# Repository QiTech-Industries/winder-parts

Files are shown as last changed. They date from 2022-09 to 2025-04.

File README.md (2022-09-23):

# Winder Parts
This repository contains a part list and .stl as well as .step files for the current version of the JARVIS WINDER.

## Build the Winder
You are welcome to build your own. You just need a 3D printer and an Amazon account :D However we have no assembly instructions. The process should be pretty self-explanatory though.

We also provide the software for it, which can be found here: https://github.com/QiTech-Industries/Winder

## Improve the Winder
In case you make an improvement to one of the parts which you think may be beneficial for others as well, you are free to open a Pull Request which we are willing to merge into main. Also improvements regarding documentation/assembly instructions are welcome.
- translate the file names and part list to english
- write assembly instructions
- make the CNC Shield screw into the electronic box
- find a better solution for ESD protection than sanding down motors and profiles so they have an electrical connection
- make an excel part list with (possibly with links for buying, automatic BOM generation?)
- make the spool axis not hang from the motor shaft
- create a full CAD model (someone deleted ours :( )
- improve the friction of the puller system
- find an alternative to the TMC based tension control
- whatever you find needs improvement...

## State of the hardware
Like your see: We know that the hardware is not perfect, especially the automatic tension adjustment with the TMC2130 drivers and the friction of the puller rolls harms production. So don't expect wonders. Nevertheless we believe that this can be a good starting point in case you want to build a filament winding machine. I mean at least we successfully produced filament with it.

## No support policy
Please be aware that we can only provide support for customers that purchased a JARVIS WINDER directly from us. We have not enough resources to offer support for people that build their own (like you maybe ;). However we do our best to publish all the documentation we made internally so it should at least be possible to "puzzle" all the parts together yourself. Feel free to improve the documentation if anything has been unclear to you.

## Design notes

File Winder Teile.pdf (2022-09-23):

Heißkleber

1

Schrumpfschlauch 3cm dünn

8

Schrumpfschlauch 15cm dick

1

Schrumpfschlauch 20cm dick

1

S+W Kabel 5cm

1

Kabelbrücke

1

Kühlkörper

3

CNC Shield

1

TMC2130

3

ESPDuino ESP32

1

# Winder Elektronik

Stepper 39mm Kabel 25cm

1

Stepper 47mm Kabel 1m

1

Stepper 1:5.18 Kabel 20cm

1

Elektronik Box Basis 30g

1

Elektronik Box Deckel 30g

1

Ferrari Achsaufnahme 8g

1

Ferrari V2 25g

1

Ferrari Motorhalter 22g

1

Puller Federaufnahme unten 1g

2

Puller Federaufnahme oben 1g

2

Puller Felge Kern 3g

1

Puller Felge rund 5g

1

Puller Felge eckig 6g

1

Puller Unterlagsscheibe dünn 1g

2

Puller Querbalken 2g

1

Puller Seite 26g

2

Puller Motor Halter 4g

1

Puller Platte 25g

1

Puller Unterlagsscheibe dick 1g

2

Laserhalter 3g

1

Spool Motor Halter 15g

1

Spoolache Hero 7g

1

Spoolachse Sidekick 36g

1

Endkappe 20x40 2 Pin 2g

1

Endkappe 40x40 4Pin 5g

1

Endkappe 20x40 4 Pin 3g

3

Hohlstange l-55

1

Hohlstange d-8 l-75 Felge bei 1,6

1

Gewindestange M8 l-125

1

Linearachse d-8 l-240

1

Gewindespindel d-8 l-210

1

Linearmutter M8 l-15 d-22

1

Gewindedübel M8x28 d-10

1

Gewindebuchse M8x13

1

Eckverbinder außen 20x20

1

Gewebeschlauch 200 u-50

1

Nutensteine M5

25

T-Slot Eckverbinder 25x25

12

Aluprofil 20x40x200

4

Gummifüße d-8

4

Aluprofil 20x40x400

2

# Winder Bauteile

Mutter M4x3

5

Mutter M3x2,5

4

Netzteil 12V min. 2A

1

Box 450x350x350

1

Hama Laser

1

Nutverkleidung l-30

1

Nutverkleidung l-320

1

Nagel d-4 l-14

2

Silikonrolle l-28 d-32 d-25

2

Extruder Feder l-20 d-7,5

2

Kugellager d-8 d-22 l-7

4

Rillenkugellager d-13 d-10 l-4

3

Flex Coupler d-8 d-5 l-25

2

Flanschlager b-55 l-29 d-8

1

Linearlager d-8 d-15 l-24

1

# Winder Bauteile

Inbusschrauben M3x20

4

Inbusschraube M4x18

6

Inbusschraube M3x8

15

Inbusschraube M3x12

10

Linsenkopf breit d-11 M5x8

4

Madenschrauben M3x6

24

Senkkopf-Kreuz l-43

4

Linsenkopfschrauben M5x8

23

# Winder Schrauben

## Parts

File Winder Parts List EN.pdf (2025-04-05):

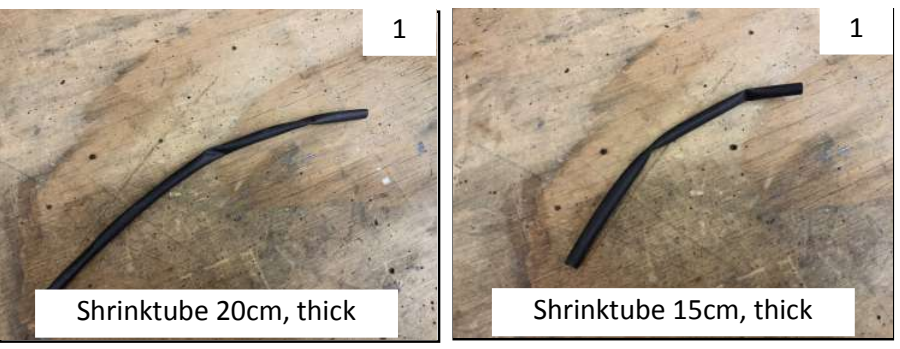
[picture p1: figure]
Shrinktube 15cm, thick; Shrinktube 20cm, thick
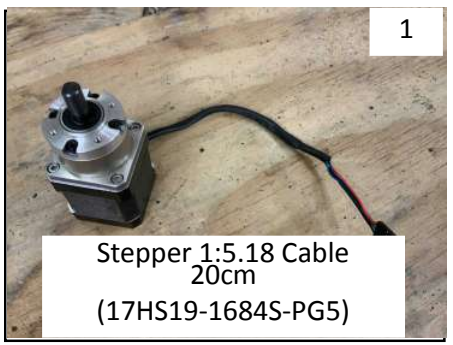
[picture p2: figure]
Stepper 1:5.18 Cable 20cm (17HS19-1684S-PG5)

Hot glue stick

1

Shrinktube 3cm, thin

8

Black+White Cable 5cm

1

Pitch Jumper Cap

1

Heat sink
(sometimes included with TMC2130)

3

A4988 Driver CNC Shield

1

TMC2130 stepper motor driver

3

ESPDuino ESP32 D1R32 Wemos

1

# Winder Electronic Parts

Stepper 47mm Cable 1m
(17HS19-2004S1)

2

Electronics Box Base 30g

1

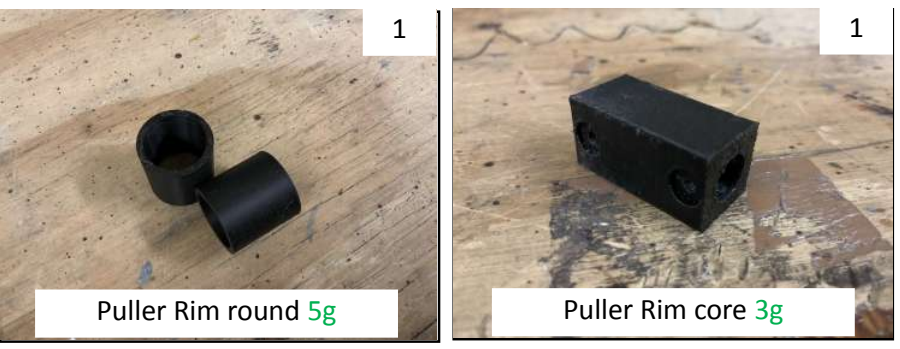
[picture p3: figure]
Puller Rim core 3g; Puller Rim round 5g

Electronics Box Lid 30g

1

Ferrari Axle Holder 8g

1

Ferrari with V-groove bearings 25g

1

Ferrari Motorholder 22g

1

Puller Spring holder Bottom 1g

2

Puller Spring Holder top 1g

2

Puller Rim square 6g

1

Puller Washer thin 1g

2

Puller Crossbar 2g

1

Puller Side 26g

2

Puller Motor Holder 4g

1

Puller Plate 25g

1

# Winder Printed Parts

Spool Motor Holder 15g

1

Spoolaxle Hero 7g

1

Spoolaxle Sidekick 36g

1

Endcap 20x40 2 Pin 2g

1

Endcap 40x40 4Pin 5g

1

Endcap 20x40 4 Pin 3g

3

# Winder Printed Parts

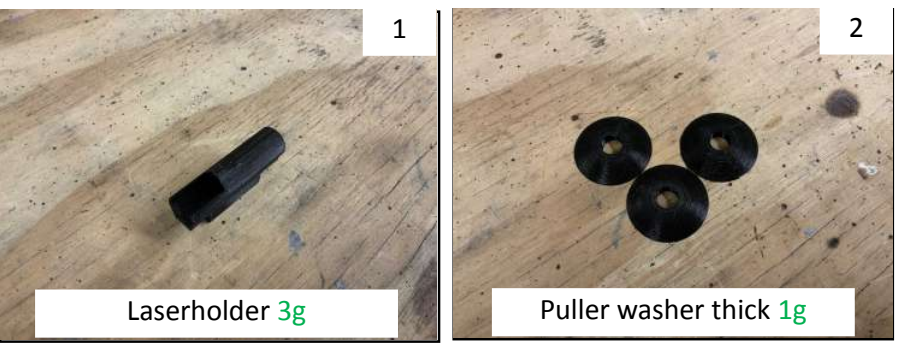
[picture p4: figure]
Puller washer thick 1g; Laserholder 3g

Hollow tube D-8 L-55

1

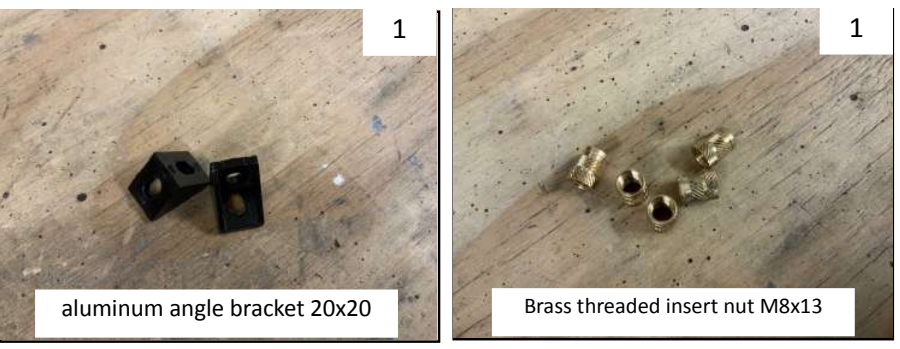
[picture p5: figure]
Brass threaded insert nut M8x13; aluminum angle bracket 20x20

Hollow tube D-8 L-75 Thickness 1.6

1

Threaded rod M8 L-125

1

Linear axle/Rod D-8 L-240

1

T8 Lead screw D-8 L-210

1

Brass nut for T8 lead
screw
M8 L-15 D-22

1

Drop in expansion anchor M8x28 OD-10

1

Braided Sleeving 200mm u-50

1

T-nut M5

25

T-slot L-type 90 degree
2020 aluminum connector
25x25

12

V-slot ALU extrusion
profile
20x40x200

4

Rubber feet D-8

4

V-slot ALU extrusion
profile
20x40x400

2

# Winder Parts

Nut M4x3

5

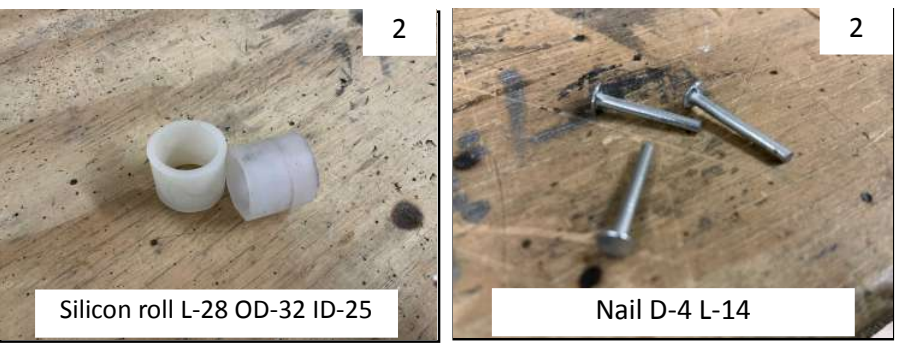
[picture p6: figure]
Nail D-4 L-14; Silicon roll L-28 OD-32 ID-25

Nut M3x2,5

4

Mains power converter to 12V min. 2A

1

Box 450x350x350

1

Hama Laser

1

Insulation sleeve l-30

1

Insulation sleeve l-320

1

Puller spring L-20 D-7,5

2

Ball bearing ID-8 OD-22 L-7 (608zz)

4

Deep groove ball bearing OD-13 ID-10 L-4

3

Flex coupler ID-8 to ID-5 L-25

2

Pillow block ball bearing KP08 8mm B-55 L-29 ID-8

1

Linear bearing ID-8 OD-15 L-24

1

# Winder Parts

Hex Socket Head Cap bolt M3x8

15

Hex Socket Head Cap bolt M3x12

10

Wide Button Head Hexagon Socket bolt D-11 M5x8

4

Hex socket set screw M3x6

24

flat head countersunk, phillips, L-43 M3

4

Button Head Hexagon Socket bolt M5x8

23

# Winder Screws & Bolts

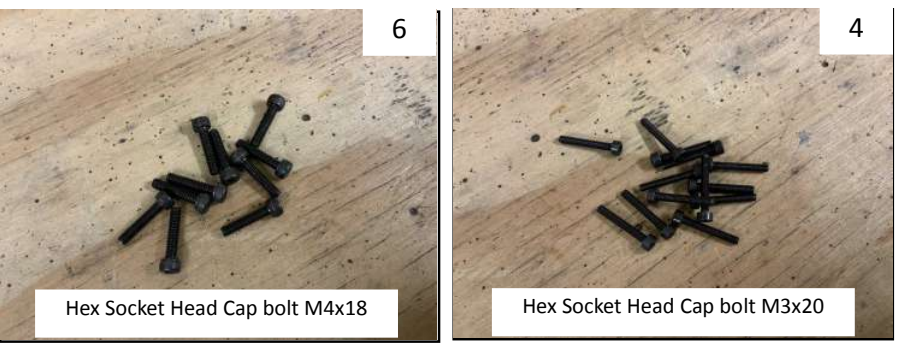
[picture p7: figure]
Hex Socket Head Cap bolt M3x20; Hex Socket Head Cap bolt M4x18

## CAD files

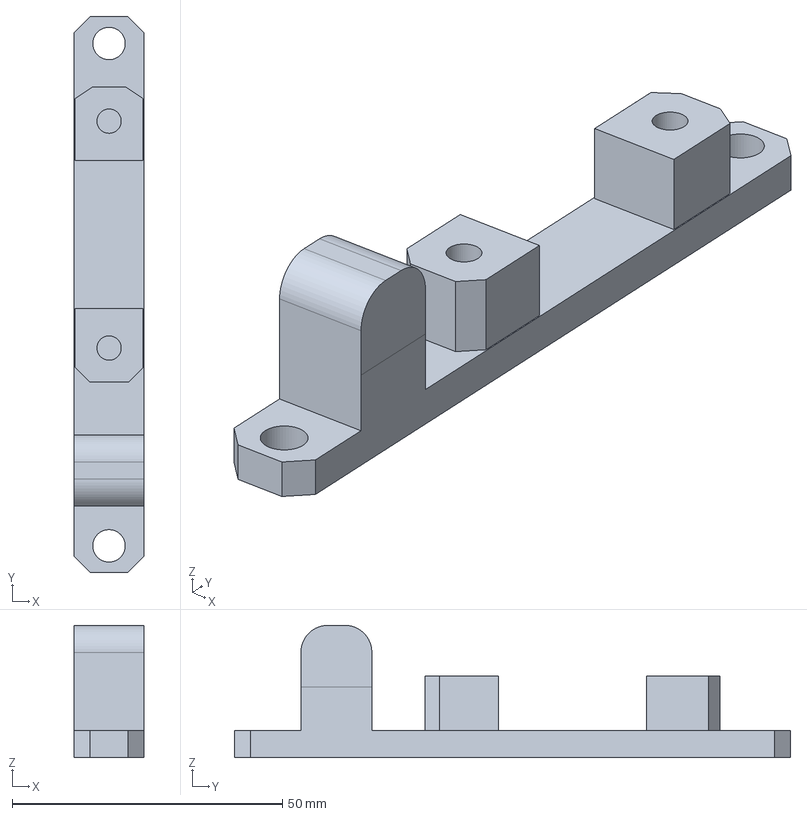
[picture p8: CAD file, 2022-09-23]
STEP/Ferrari Achsaufnahme.step
13.0 x 102.9 x 24.5 mm

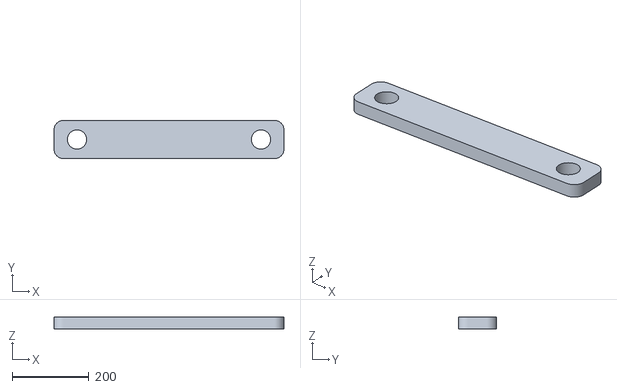
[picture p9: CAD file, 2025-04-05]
STL/STL-EN-UPDATED/Puller Crossbar.stl
600.0 x 99.8 x 30.0

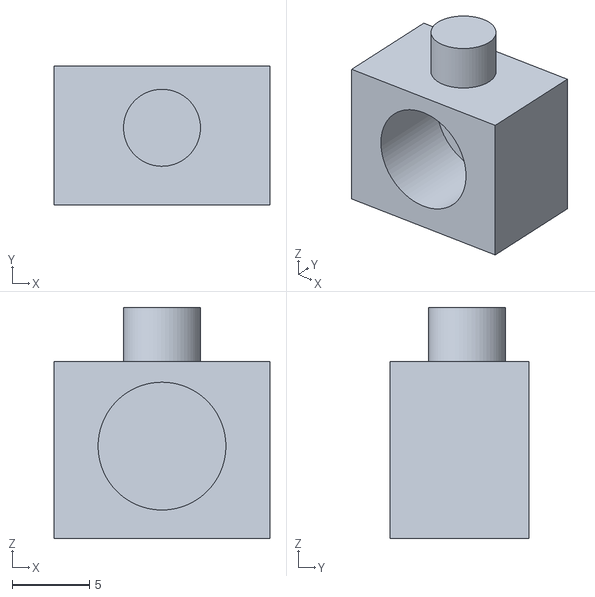
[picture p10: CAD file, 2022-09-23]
STL/STL-GER-ORIGINAL/Puller Federaufnahme unten.stl
14.0 x 9.00 x 15.0

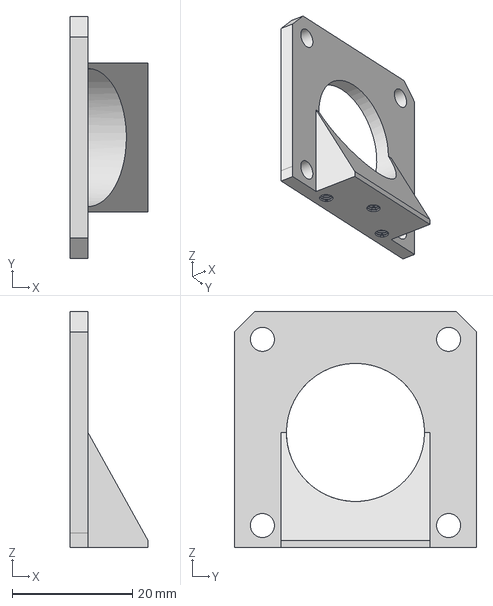
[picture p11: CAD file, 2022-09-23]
STEP/Puller Motor Halter.step
13.0 x 40.3 x 39.3 mm

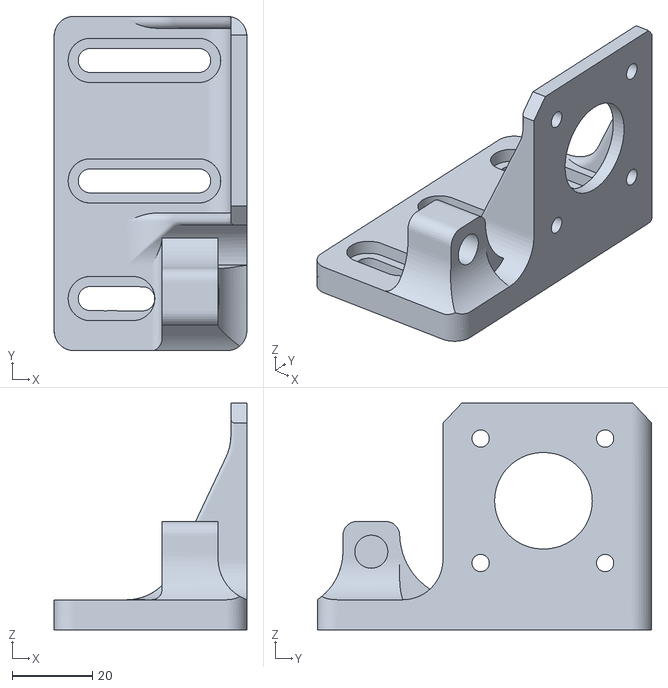
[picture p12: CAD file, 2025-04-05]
STL/STL-EN-UPDATED/Ferrari Motor Holder.stl
48.0 x 83.3 x 56.5

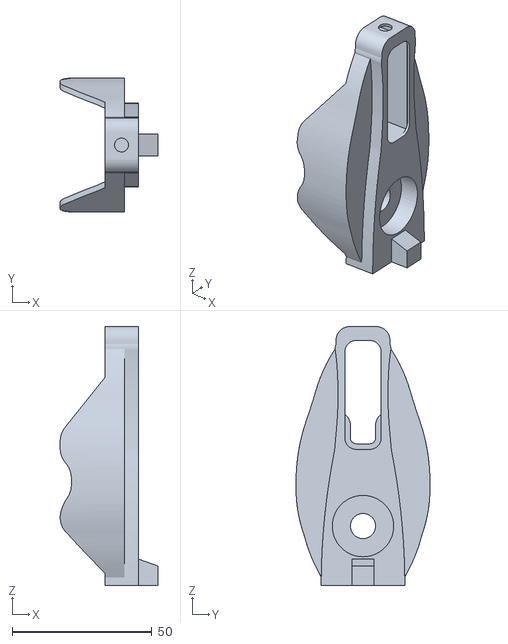
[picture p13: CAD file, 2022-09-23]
STL/STL-GER-ORIGINAL/Puller Seite Rechts.stl
35.0 x 48.0 x 92.8

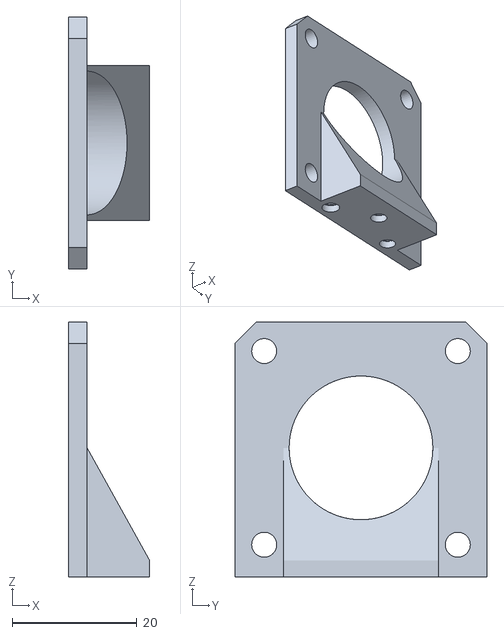
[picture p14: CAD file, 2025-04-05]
STL/STL-EN-UPDATED/Puller Motor Holder.stl
13.0 x 40.3 x 40.8

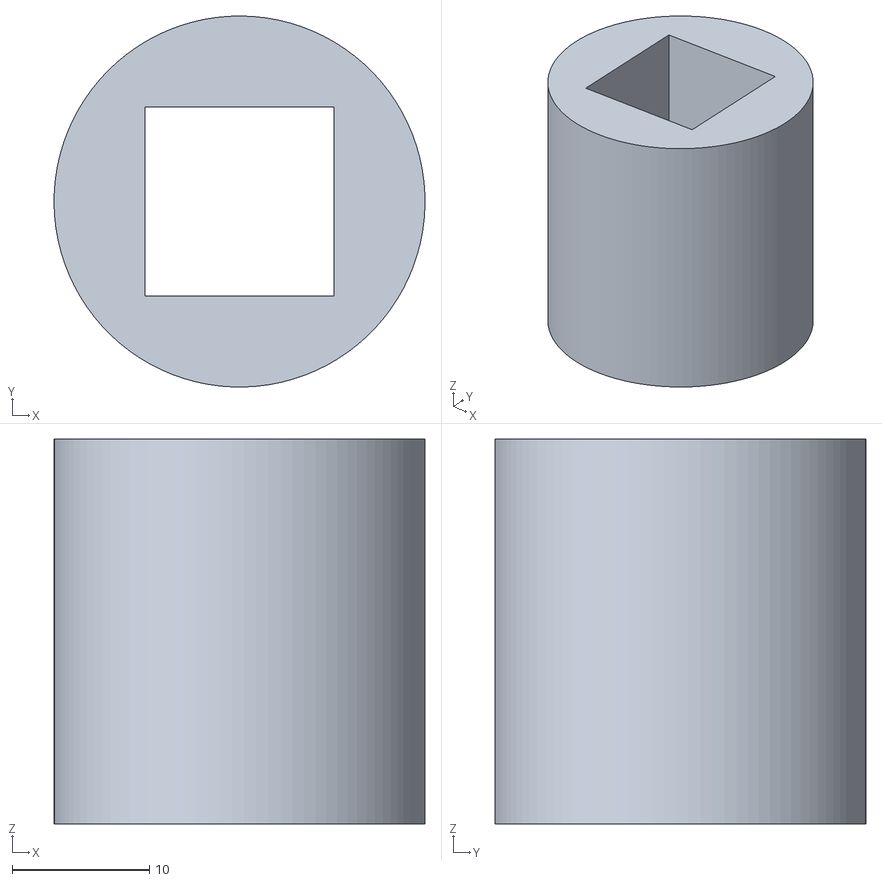
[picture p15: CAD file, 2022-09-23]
STL/STL-GER-ORIGINAL/Puller Felge eckig.stl
27.0 x 27.0 x 28.0

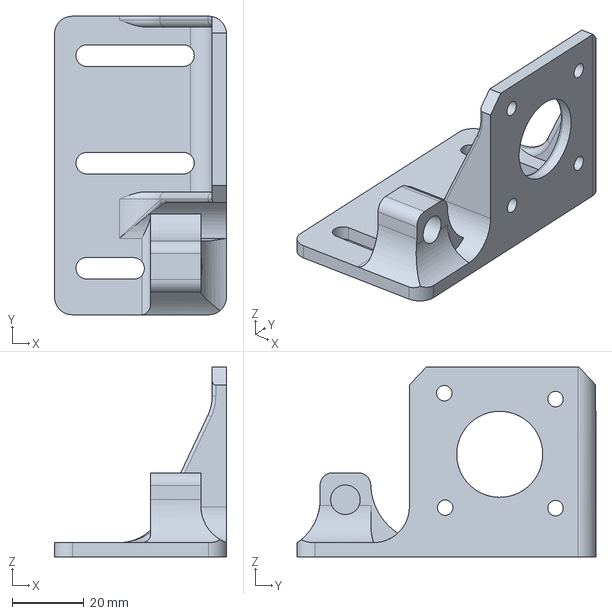
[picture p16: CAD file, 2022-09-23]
STEP/Ferrari Motorhalter.step
48.0 x 83.3 x 53.0 mm

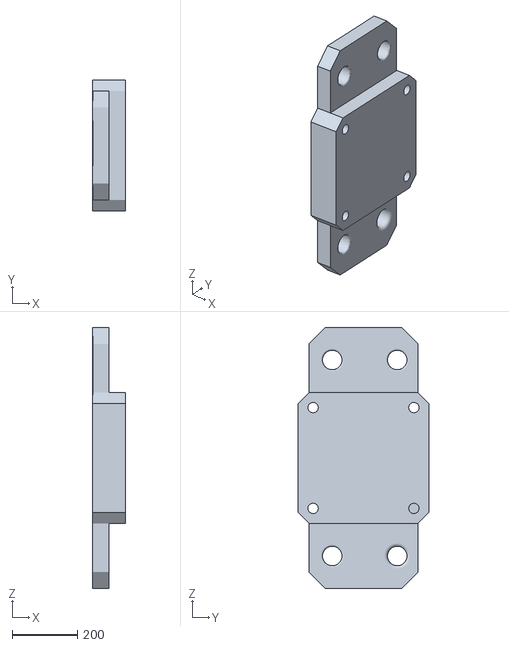
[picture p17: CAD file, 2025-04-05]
STL/STL-EN-UPDATED/Spool Motor Holder.stl
100.0 x 403.0 x 803.0

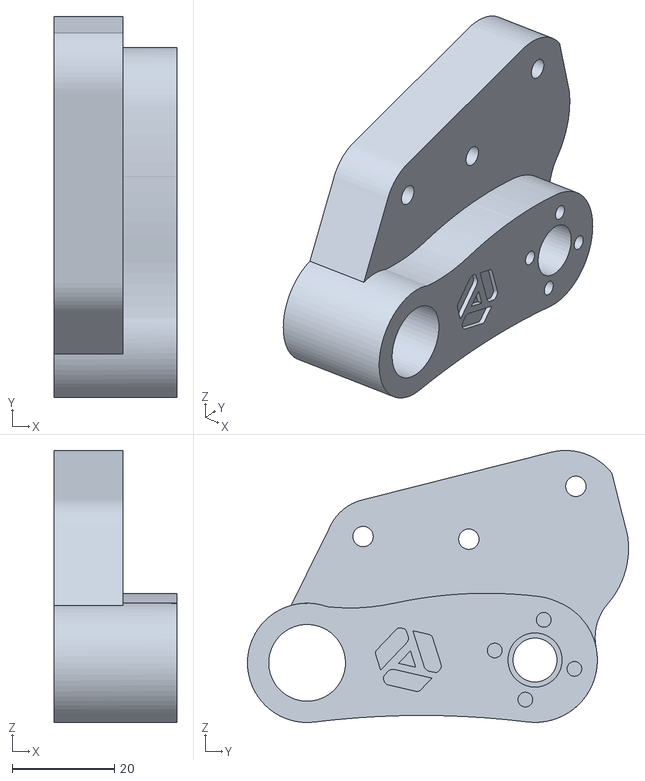
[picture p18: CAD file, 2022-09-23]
STL/STL-GER-ORIGINAL/Filamentferrarie mit Kugellagern.stl
24.0 x 74.5 x 53.2

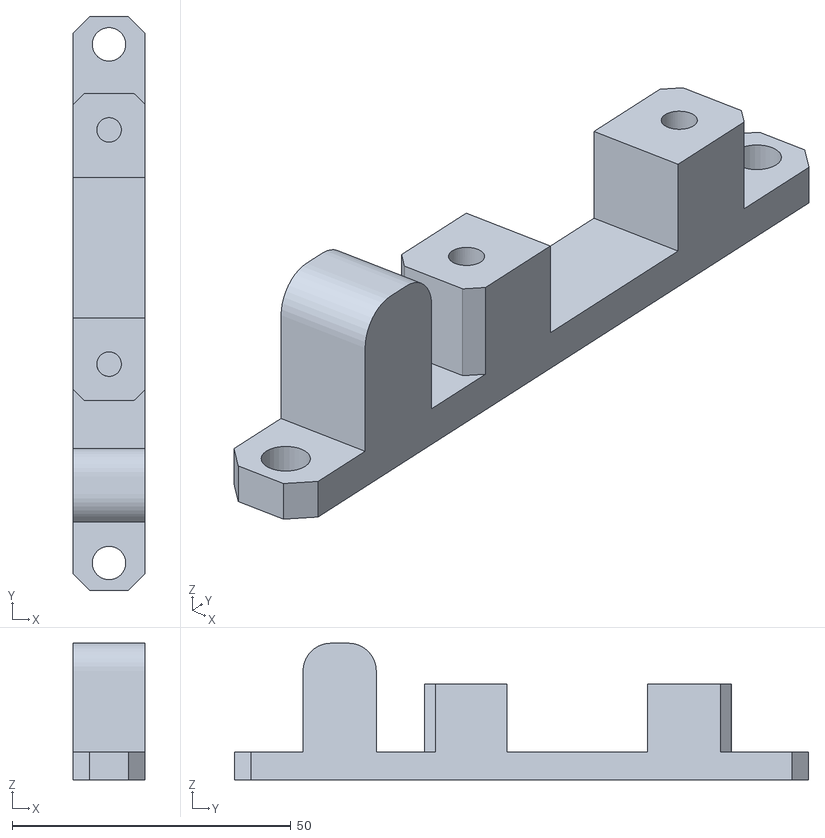
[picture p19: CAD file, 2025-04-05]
STL/STL-EN-UPDATED/Ferrari Axle Holder.stl
13.0 x 102.9 x 24.5

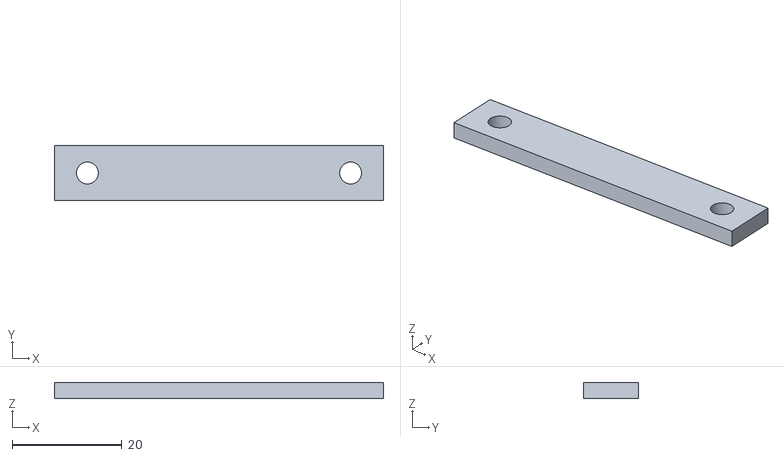
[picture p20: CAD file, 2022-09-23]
STL/STL-GER-ORIGINAL/Puller Querbalken.stl
60.0 x 9.98 x 3.00

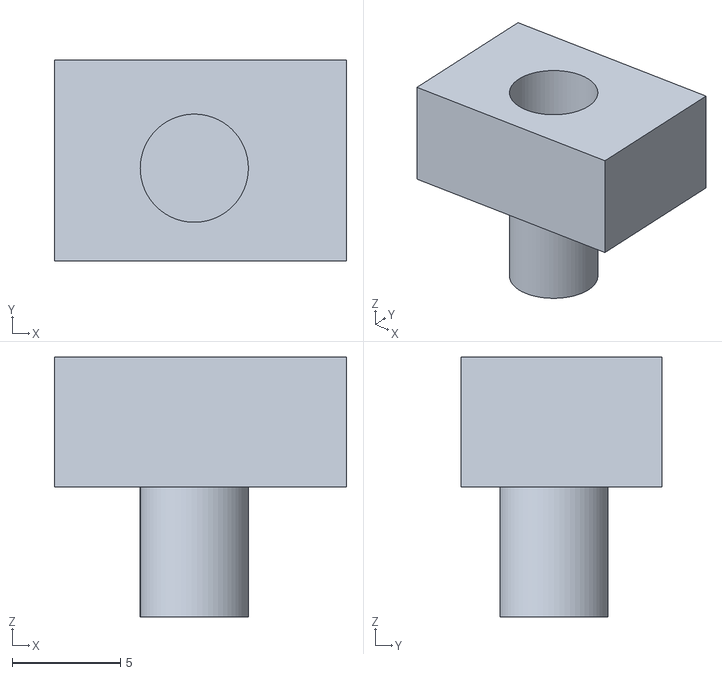
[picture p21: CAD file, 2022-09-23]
STL/STL-GER-ORIGINAL/Puller Federaufnahme oben.stl
13.5 x 9.29 x 12.0

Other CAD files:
STEP/Puller Federaufnahme unten.step
STEP/Puller Seite Links.step
STEP/Puller Rolle.step
STL/STL-EN-UPDATED/Puller Side L.stl
STEP/Elektronik Box Basis.step
STEP/Elektronik Box Deckel.step
STEP/Endkappe 20x40 2 Pin.step
STEP/Endkappe 20x40 4 Pin.step
STEP/Endkappe 40x40 4 Pin.step
STEP/Filamentferrarie mit Kugellagern.step
STEP/Puller Achsaufnahme.step
STEP/Puller Federaufnahme oben.step
STEP/Puller Felge eckig.step
STEP/Puller Platte.step
STEP/Puller Querbalken.step
STEP/Puller Seite Rechts.step
STEP/Puller Unterlagsscheiben.step
STEP/Spoolachse Hero.step
STEP/Spoolachse Sidekick.step
STEP/Spulen Motor Halter.step
STL/STL-EN-UPDATED/Electronics Box Base.stl
STL/STL-EN-UPDATED/Electronics Box Lid.stl
STL/STL-EN-UPDATED/Endcap 20x40 2 Pin.stl
STL/STL-EN-UPDATED/Endcap 20x40 4 Pin.stl
STL/STL-EN-UPDATED/Endcap 40x40 4 Pin.stl
STL/STL-EN-UPDATED/Puller Plate.stl
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

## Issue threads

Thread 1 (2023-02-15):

Missing parts

3DGera, 2023-02-15:
Hello qitech Team,

unfortunately I can't find the printed Parts for the "Filament Ferrari" and the "Laser Attachment".

I need your Winder to rewind Filament Rolls because they don't fit in the BambuLab AMS :(

Thanks

3DGera, 2023-03-29:
I spoke to the developers and the parts are not missing after all. The filament Ferrari is realized here with 3 screws.

Closed 2023-03-29.

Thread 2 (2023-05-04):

Missing STL Files

3dman74, 2023-05-04:
If i check your documentation and overview of the parts i show that some STL Files not online.
Laser Mount and  Spacer files can you update ? Thanks

DreiDe, 2024-05-15:
We changed the version of the laser a couple of times. For the currently uploaded file versions we don't have the matching  laser mount anymore. Either you have to remodel it yourself or you calibrate by eye. Works well most of the time. Same for the spacer.

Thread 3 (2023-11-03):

Need Wiring Diagram

CornDogLover999, 2023-11-03:
Is there a wiring diagram for this?  I need one as I can't determine if one of my components is fatly or not.  I am also making a step by step guide on how to assembly this but need to get it working first before I upload.  Cannot get any steppers to work, am getting no movement.

DreiDe, 2024-05-15:
@CornDogLover999 We used this spreadsheet for wiring: https://github.com/QiTech-Industries/Winder/blob/main/images/IMG_1544.jpeg

CornDogLover999, 2024-05-21:
Thank You!

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

Closed 2024-05-26.

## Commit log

2022-09-23 add documentation for all the hardware parts
    [Elektronik Box Basis.step, Elektronik Box Basis.stl, Elektronik Box Deckel.step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]
2025-03-18 Updated geometry to fix axis alignment
    Updated Parts:
    -Ferrari Motor Holder
    -Ferrari Axle Holder
    -Puller crossbar
    -Puller Motor Holder
    [Electronics Box Base.stl, Electronics Box Lid.stl, Endcap 20x40 2 Pin.stl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]
2025-03-18 Original STL's with German names
    [Elektronik Box Basis.stl, Elektronik Box Deckel.stl, Endkappe 20x40 2 Pin.stl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]
